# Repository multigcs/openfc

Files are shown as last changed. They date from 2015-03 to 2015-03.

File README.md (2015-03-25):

OpenFC is an new Open-Hardware Flight-Controller

Standard-Size: 50x50mm (45x45mm holes) 

CPU: STM32F405 @ 168MHZ

Gyro/ACC: MPU6000 (SPI)

Compass: HMC5983 (SPI)

Baro: MS5611 (SPI)

Serial-Ports for GPS, Telemetry and SBUS

8 PWM-ESC-Connectors + CAN-Bus

PPM and SBUS inputs

microSD slot

Autoquad software compatible (Board M4r6) (https://code.google.com/p/autoquad/)

Changes v0.9:

	* initial Version
	* 2 errors in the Layout, but working

Changes v0.91: 

	* untested
	* bugfixes of v0.9
	* LED-Postion moved
	* SBUS-Inverter added

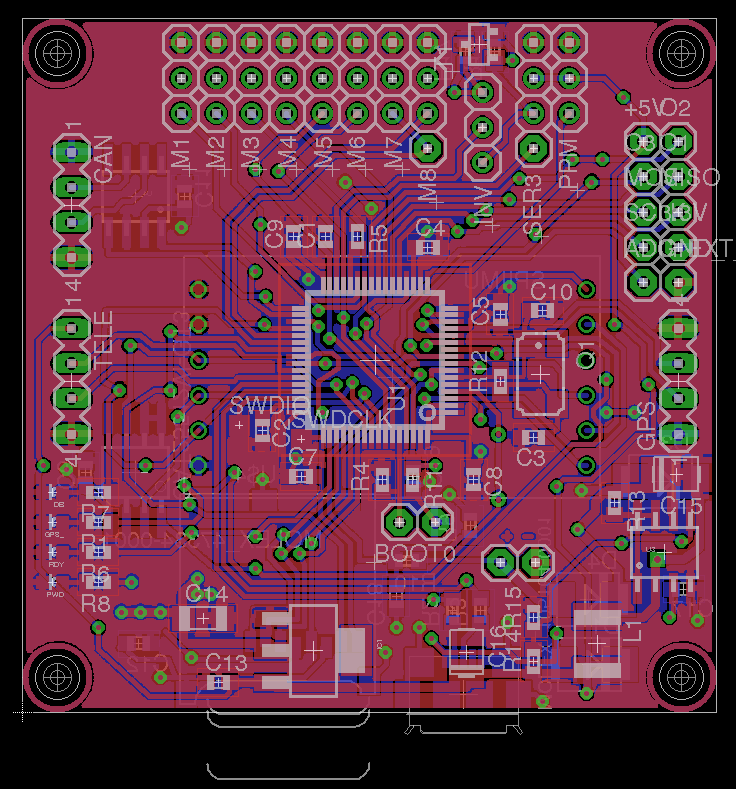
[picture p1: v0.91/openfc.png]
v0.91 Board-Layout


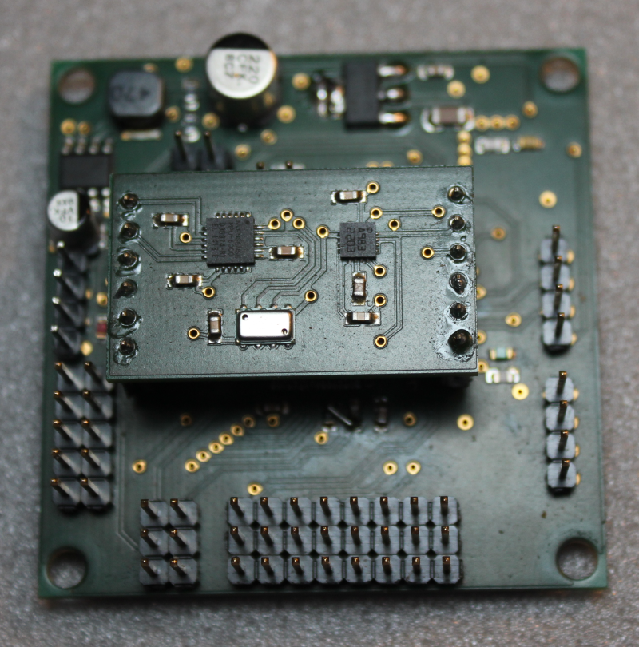
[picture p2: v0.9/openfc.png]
v0.90 Board-Layout v0.9 Board


First IMU-Test: https://www.youtube.com/watch?v=cWaLLEZJb3Y

First Flight-Test: https://www.youtube.com/watch?v=trHpGgnNXYM

First Poshold-Test: https://www.youtube.com/watch?v=XDp27G_Ods4

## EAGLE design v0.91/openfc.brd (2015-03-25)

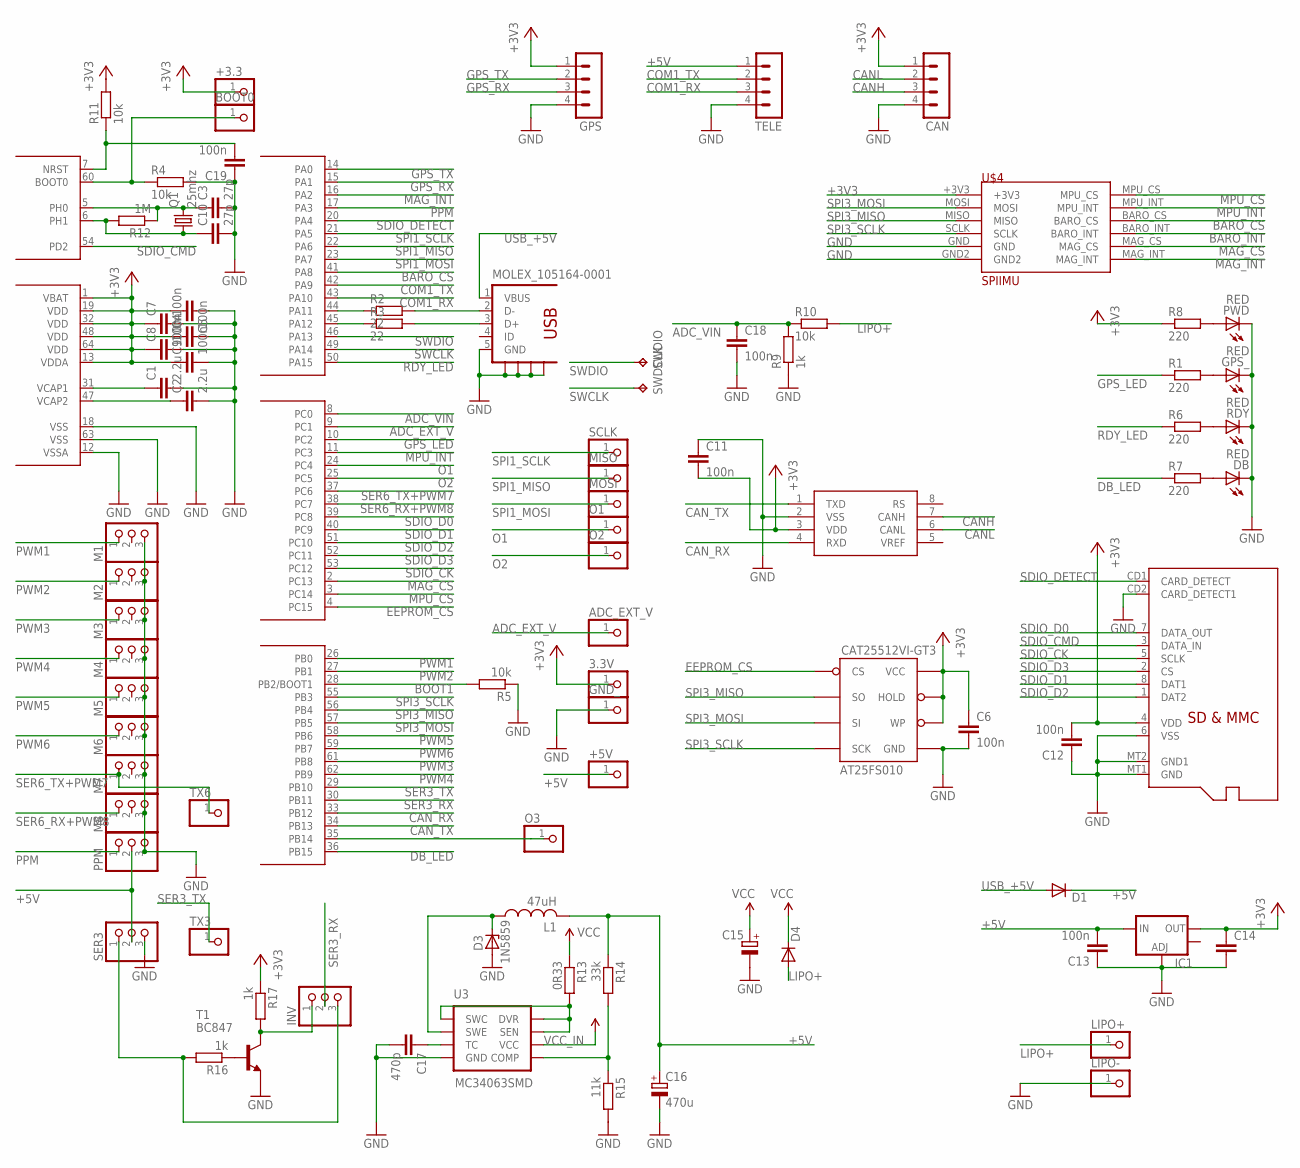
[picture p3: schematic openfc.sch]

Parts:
3.3V: PINHD-1X1; 1X01
+3.3, +5V: PINHD-1X1; 1X01
ADC_EXT_V: PINHD-1X1; 1X01
BOOT0: PINHD-1X1; 1X01
C1, C2: 2.2u; C0603
C3, C10: 27p; C0603
C4, C5, C6, C7, C8, C9, C11, C12, C13, C18, C19: 100n; C0603
C14: C-EUC1206; C1206
C15: CPOL-EUB/3528-21R; B/3528-21R
C16: 470u; B/3528-21R
C17: 470p; C0603
CAN: MA04-1
CAT25512VI-GT3: AT25FS010; SO08WIDE
D1, D4: DIODE-SMB; SMB
D3: 1N5859; SMB
DB: RED; LED-0603
GND_: PINHD-1X1; 1X01
GPS: MA04-1
GPS_: RED; LED-0603
IC1: V_REG_LM1117SOT223; SOT223
INV: PINHD-1X3; 1X03
L1: 47uH; L1812
LIPO+: PINHD-1X1; 1X01
LIPO-: PINHD-1X1; 1X01
M1, M2, M3, M4, M5, M6, M7, M8: PINHD-1X3; 1X03
MISO: PINHD-1X1; 1X01
MOLEX_47334-0001: MICROSD
MOLEX_105164-0001: USB-5P; USB-MINI-B
MOSI: PINHD-1X1; 1X01
O1, O2, O3: PINHD-1X1; 1X01
PPM: PINHD-1X3; 1X03
PWD: RED; LED-0603
Q1: 25mhz; CTS406
R1, R6, R7, R8: 220; R0603
R2, R3: 22; R0603
R4, R5, R10, R11: 10k; R0603
R9, R16, R17: 1k; R0603
R12: 1M; R0603
R13: 0R33; R0603
R14: 33k; R0603
R15: 11k; R0603
RDY: RED; LED-0603
SCLK: PINHD-1X1; 1X01
SER3: PINHD-1X3; 1X03
SWDCLK: TPTP14SQ; TP14SQ
SWDIO: TPTP14SQ; TP14SQ
T1: BC847; SOT23
TELE: MA04-1
TX3, TX6: PINHD-1X1; 1X01
U1: STM32F4-64; SQFP-S-10X10-64
U3: MC34063SMD; SO08
U4: MCP2551; SO08
U$4: SPIIMU

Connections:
+3V3: 3.3V.1, +3.3.1, C4.1, C5.2, C6.1, C7.1, C8.1, C9.1, C11.2, C12.2, C14.1, CAN.1, CAT25512VI-GT3.3 (WP), CAT25512VI-GT3.7 (HOLD), CAT25512VI-GT3.8 (VCC), GPS.1, IC1.2 (OUT), MOLEX_47334-0001.4 (VDD), R8.1, R11.2, R17.1, U1.1 (VBAT), U1.13 (VDDA), U1.19 (VDD), U1.32 (VDD), U1.48 (VDD), U1.64 (VDD), U4.3 (VDD), U$4.+3V3
+5V: +5V.1, C13.2, C16.+, D1.C, IC1.3 (IN), L1.2, PPM.2, R14.1, SER3.2, TELE.1
ADC_EXT_V: ADC_EXT_V.1, U1.9 (PC1)
ADC_VIN: C18.1, R9.2, R10.1, U1.8 (PC0)
BARO_CS: U1.41 (PA8), U$4.BARO_CS
BARO_INT: U$4.BARO_INT
BOOT0: BOOT0.1, R4.1, U1.60 (BOOT0)
BOOT1: R5.2, U1.28 (PB2/BOOT1)
CANH: CAN.3, U4.7 (CANH)
CANL: CAN.2, U4.6 (CANL)
CAN_RX: U1.33 (PB12), U4.4 (RXD)
CAN_TX: U1.34 (PB13), U4.1 (TXD)
COM1_RX: TELE.3, U1.43 (PA10)
COM1_TX: TELE.2, U1.42 (PA9)
DB_LED: R7.1, U1.36 (PB15)
EEPROM_CS: CAT25512VI-GT3.1 (CS), U1.4 (PC15)
GND: C1.2, C2.2, C3.2, C4.2, C5.1, C6.2, C7.2, C8.2, C9.2, C10.2, C11.1, C12.1, C13.1, C14.2, C15.-, C16.-, C17.2, C18.2, C19.1, CAN.4, CAT25512VI-GT3.4 (GND), D3.A, DB.C, GND_.1, GPS.4, GPS_.C, IC1.1 (ADJ), LIPO-.1, M1.3, M2.3, M3.3, M4.3, M5.3, M6.3, M7.3, M8.3, MOLEX_47334-0001.6 (VSS), MOLEX_47334-0001.CD2 (CARD_DETECT1), MOLEX_47334-0001.MT1 (GND), MOLEX_47334-0001.MT2 (GND1), MOLEX_105164-0001.5 (GND), MOLEX_105164-0001.S1, MOLEX_105164-0001.S2, MOLEX_105164-0001.S3, MOLEX_105164-0001.S4, PPM.3, PWD.C, R4.2, R5.1, R9.1, R15.2, RDY.C, SER3.3, T1.2 (E), TELE.4, U1.12 (VSSA), U1.18 (VSS), U1.63 (VSS), U3.4 (GND), U4.2 (VSS), U$4.GND, U$4.GND2
GPS_LED: R1.1, U1.10 (PC2)
GPS_RX: GPS.3, U1.15 (PA1)
GPS_TX: GPS.2, U1.14 (PA0)
LIPO+: D4.A, LIPO+.1, R10.2
MAG_CS: U1.2 (PC13), U$4.MAG_CS
MAG_INT: U1.16 (PA2), U$4.MAG_INT
MPU_CS: U1.3 (PC14), U$4.MPU_CS
MPU_INT: U1.11 (PC3), U$4.MPU_INT
unnamed: C2.1, U1.47 (VCAP2)
unnamed: C1.1, U1.31 (VCAP1)
unnamed: C19.2, R11.1, U1.7 (NRST)
unnamed: PWD.A, R8.2
unnamed: GPS_.A, R1.2
unnamed: R6.2, RDY.A
unnamed: DB.A, R7.2
unnamed: R16.1, T1.1 (B)
unnamed: C3.1, Q1.3 (2), R12.1, U1.5 (PH0)
unnamed: C10.1, Q1.1, R12.2, U1.6 (PH1)
unnamed: R2.1, U1.44 (PA11)
unnamed: R3.1, U1.45 (PA12)
unnamed: C17.1, U3.3 (TC)
unnamed: D3.C, L1.1, U3.2 (SWE)
unnamed: R14.2, R15.1, U3.5 (COMP)
unnamed: R13.2, U3.1 (SWC), U3.7 (SEN), U3.8 (DVR)
O1: O1.1, U1.24 (PC4)
O2: O2.1, U1.25 (PC5)
O3: O3.1, U1.35 (PB14)
PPM: PPM.1, U1.17 (PA3)
PWM1: M1.1, U1.26 (PB0)
PWM2: M2.1, U1.27 (PB1)
PWM3: M3.1, U1.61 (PB8)
PWM4: M4.1, U1.62 (PB9)
PWM5: M5.1, U1.58 (PB6)
PWM6: M6.1, U1.59 (PB7)
RDY_LED: R6.1, U1.50 (PA15)
SDIO_CK: MOLEX_47334-0001.5 (SCLK), U1.53 (PC12)
SDIO_CMD: MOLEX_47334-0001.3 (DATA_IN), U1.54 (PD2)
SDIO_D0: MOLEX_47334-0001.7 (DATA_OUT), U1.39 (PC8)
SDIO_D1: MOLEX_47334-0001.8 (DAT1), U1.40 (PC9)
SDIO_D2: MOLEX_47334-0001.1 (DAT2), U1.51 (PC10)
SDIO_D3: MOLEX_47334-0001.2 (CS), U1.52 (PC11)
SDIO_DETECT: MOLEX_47334-0001.CD1 (CARD_DETECT), U1.20 (PA4)
SER3_RX: INV.2, U1.30 (PB11)
SER3_RX_INV: INV.1, R17.2, T1.3 (C)
SER3_RX_NORM: INV.3, R16.2, SER3.1
SER3_TX: TX3.1, U1.29 (PB10)
SER6_RX+PWM8: M8.1, U1.38 (PC7)
SER6_TX+PWM7: M7.1, TX6.1, U1.37 (PC6)
SPI1_MISO: MISO.1, U1.22 (PA6)
SPI1_MOSI: MOSI.1, U1.23 (PA7)
SPI1_SCLK: SCLK.1, U1.21 (PA5)
SPI3_MISO: CAT25512VI-GT3.2 (SO), U1.56 (PB4), U$4.MISO
SPI3_MOSI: CAT25512VI-GT3.5 (SI), U1.57 (PB5), U$4.MOSI
SPI3_SCLK: CAT25512VI-GT3.6 (SCK), U1.55 (PB3), U$4.SCLK
SWCLK: SWDCLK.TP, U1.49 (PA14)
SWDIO: SWDIO.TP, U1.46 (PA13)
USB_+5V: D1.A, MOLEX_105164-0001.1 (VBUS)
USB_D+: MOLEX_105164-0001.3 (D+), R3.2
USB_D-: MOLEX_105164-0001.2 (D-), R2.2
VCC_IN: C15.+, D4.C, R13.1, U3.6 (VCC)

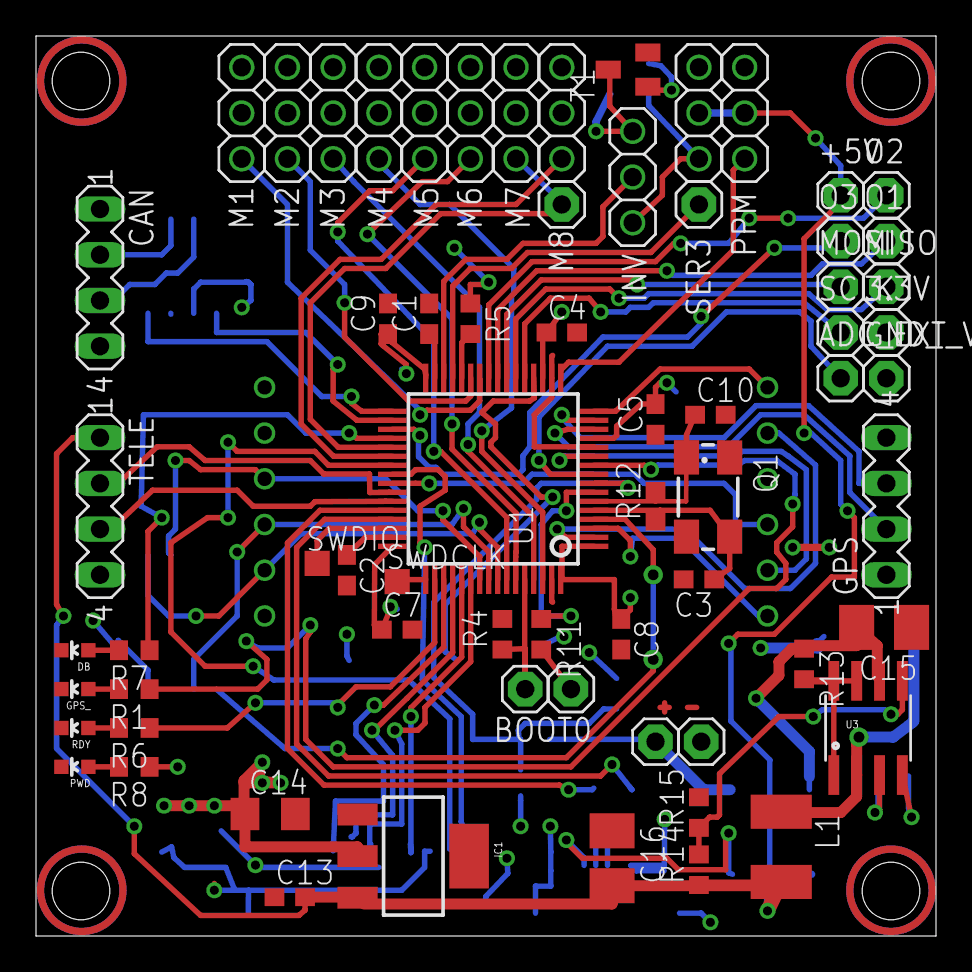
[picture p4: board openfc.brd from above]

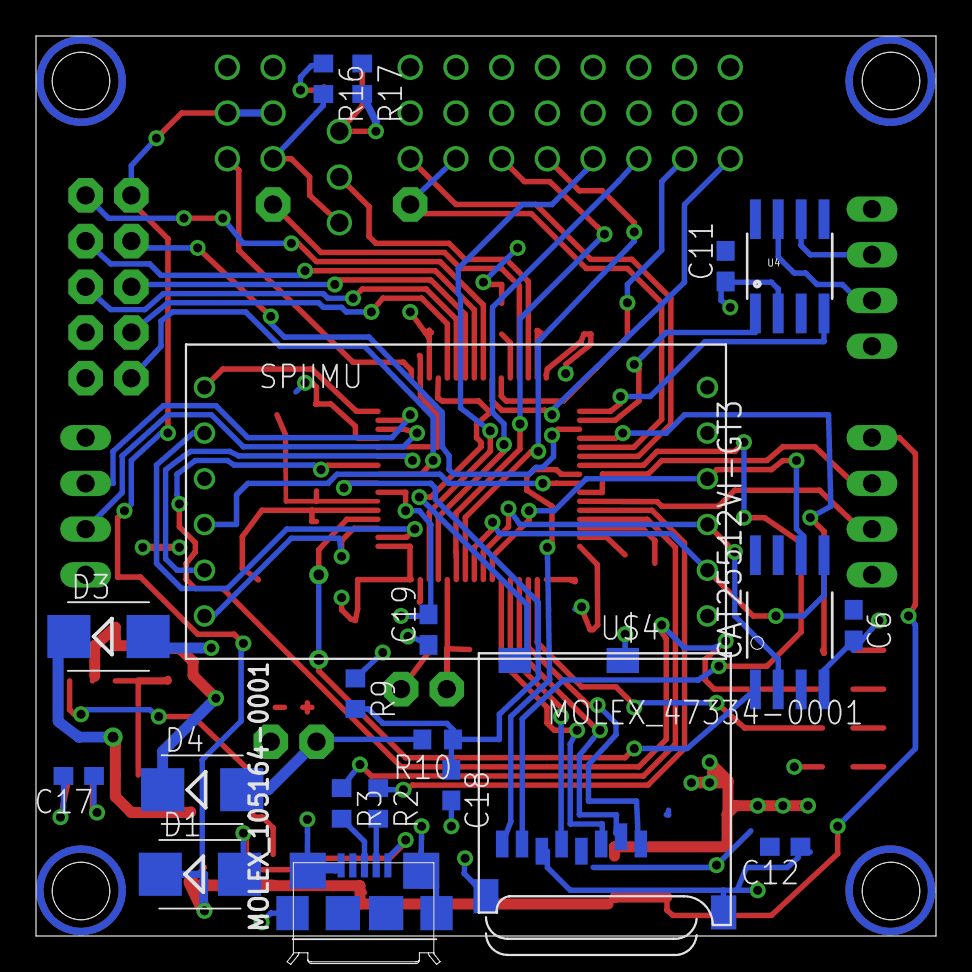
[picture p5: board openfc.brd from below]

Board: 2 copper layers, 50.0 x 50.0 mm, 86 parts (20 on the bottom side), 76 nets.

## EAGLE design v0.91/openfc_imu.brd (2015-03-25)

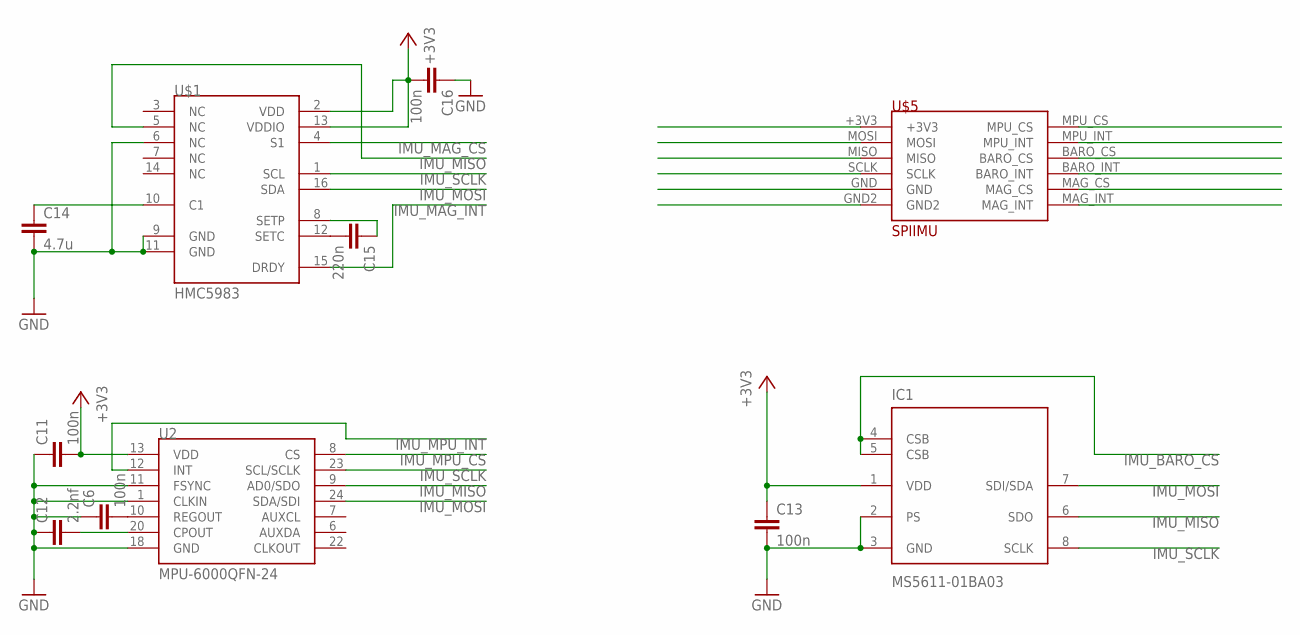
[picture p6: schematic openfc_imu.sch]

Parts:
C6, C11, C13, C16: 100n; C0603
C12: 2.2nf; C0603
C14: 4.7u; C0603
C15: 220n; C0603
IC1: MS5611-01BA03; SON125P300X500X100-8N
U2: MPU-6000QFN-24; QFN-24-TESTING
U$1: HMC5983; 16LPCC
U$5: SPIIMU

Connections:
IMU+3V3: C11.2, C13.1, C16.2, IC1.1 (VDD), U2.13 (VDD), U$1.2 (VDD), U$1.13 (VDDIO), U$5.+3V3
IMU_BARO_CS: IC1.4 (CSB), IC1.5 (CSB), U$5.BARO_CS
IMU_BARO_INT: U$5.BARO_INT
IMU_GND: C6.1, C11.1, C12.1, C13.2, C14.2, C16.1, IC1.2 (PS), IC1.3 (GND), U2.1 (CLKIN), U2.11 (FSYNC), U2.18 (GND), U$1.6 (NC), U$1.9 (GND), U$1.11 (GND), U$5.GND, U$5.GND2
IMU_MAG_CS: U$1.4 (S1), U$5.MAG_CS
IMU_MAG_INT: U$1.15 (DRDY), U$5.MAG_INT
IMU_MISO: IC1.6 (SDO), U2.9 (AD0/SDO), U$1.5 (NC), U$5.MISO
IMU_MOSI: IC1.7 (SDI/SDA), U2.24 (SDA/SDI), U$1.16 (SDA), U$5.MOSI
IMU_MPU_CS: U2.8 (CS), U$5.MPU_CS
IMU_MPU_INT: U2.12 (INT), U$5.MPU_INT
IMU_SCLK: IC1.8 (SCLK), U2.23 (SCL/SCLK), U$1.1 (SCL), U$5.SCLK
unnamed: C6.2, U2.10 (REGOUT)
unnamed: C14.1, U$1.10 (C1)
unnamed: C12.2, U2.20 (CPOUT)
unnamed: C15.1, U$1.8 (SETP)
unnamed: C15.2, U$1.12 (SETC)

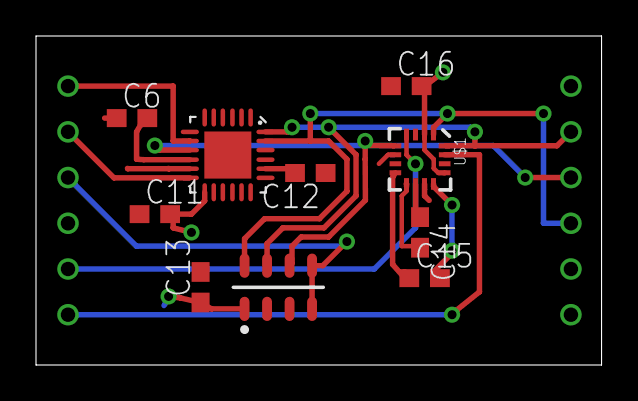
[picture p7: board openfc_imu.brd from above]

Board: 2 copper layers, 31.4 x 18.3 mm, 11 parts (1 on the bottom side), 15 nets.

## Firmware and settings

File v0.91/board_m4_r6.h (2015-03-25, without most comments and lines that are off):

#define _board_h
#define HAS_USB
#define SDIO_DMA			DMA2
#define SDIO_DMA_STREAM			DMA2_Stream3
#define SDIO_DMA_CHANNEL		DMA_Channel_4
#define SDIO_DMA_FLAG_FEIF		DMA_FLAG_FEIF3
#define SDIO_DMA_FLAG_DMEIF		DMA_FLAG_DMEIF3
#define SDIO_DMA_FLAG_TEIF		DMA_FLAG_TEIF3
#define SDIO_DMA_FLAG_HTIF		DMA_FLAG_HTIF3
#define SDIO_DMA_FLAG_TCIF		DMA_FLAG_TCIF3
#define SDIO_DMA_IRQHANDLER		DMA2_Stream3_IRQHandler
#define SDIO_DMA_IRQn			DMA2_Stream3_IRQn
#define SDIO_DETECT_GPIO_PORT		GPIOA
#define SDIO_DETECT_PIN			GPIO_Pin_4
#define SDIO_DETECT_PORT_SOURCE		EXTI_PortSourceGPIOA
#define SDIO_DETECT_PIN_SOURCE		EXTI_PinSource4
#define SDIO_DETECT_IRQ			EXTI4_IRQn
#define SDIO_DETECT_HANDLER		EXTI4_IRQHandler
#define SDIO_DETECT_EXTI_LINE		EXTI_Line4
#define SDIO_TRANSFER_CLK_DIV           ((uint8_t)0x02)	// SDIO Data Transfer Frequency (12MHz max)
enum pwmPorts {
    PWM_1 = 0,
    PWM_2,
    PWM_3,
    PWM_4,
    PWM_5,
    PWM_6,
    PWM_7,
    PWM_8,
    PWM_9,
    PWM_NUM_PORTS
};
#define PPM_PWM_CHANNEL		8	// which PWM channel to use for PPM capture
#define PWM_TIMERS  const TIM_TypeDef *pwmTimers[] = { \
    TIM3, \
    TIM3, \
    TIM4, \
    TIM4, \
    TIM4, \
    TIM4, \
    TIM8, \
    TIM8, \
    TIM9 \
};
#define	PWM_AFS	    const uint8_t pwmAFs[] = { \
    GPIO_AF_TIM3, \
    GPIO_AF_TIM3, \
    GPIO_AF_TIM4, \
    GPIO_AF_TIM4,  \
    GPIO_AF_TIM4, \
    GPIO_AF_TIM4, \
    GPIO_AF_TIM8, \
    GPIO_AF_TIM8, \
    GPIO_AF_TIM9  \
};
#define PWM_PORTS   const GPIO_TypeDef *pwmPorts[] = { \
    GPIOB, \
    GPIOB, \
    GPIOB, \
    GPIOB, \
    GPIOB, \
    GPIOB, \
    GPIOC, \
    GPIOC, \
    GPIOA  \
};
#define PWM_PINS    const uint32_t pwmPins[] = { \
    GPIO_Pin_0, \
    GPIO_Pin_1, \
    GPIO_Pin_8, \
    GPIO_Pin_9, \
    GPIO_Pin_6, \
    GPIO_Pin_7, \
    GPIO_Pin_6, \
    GPIO_Pin_7, \
    GPIO_Pin_3 \
};
#define PWM_PINSOURCES	const uint16_t pwmPinSources[] = { \
    GPIO_PinSource0, \
    GPIO_PinSource1, \
    GPIO_PinSource8, \
    GPIO_PinSource9, \
    GPIO_PinSource6, \
    GPIO_PinSource7, \
    GPIO_PinSource6, \
    GPIO_PinSource7, \
    GPIO_PinSource3 \
};
#define PWM_TIMERCHANNELS   const uint8_t pwmTimerChannels[] = { \
    TIM_Channel_3, \
    TIM_Channel_4, \
    TIM_Channel_3, \
    TIM_Channel_4, \
    TIM_Channel_1, \
    TIM_Channel_2, \
    TIM_Channel_1, \
    TIM_Channel_2, \
    TIM_Channel_2 \
};
#define PWM_BDTRS   const uint8_t pwmBDTRs[] = { \
    0, \
    0, \
    0, \
    0, \
    0, \
    0, \
    1, \
    1, \
    0 \
};
#define PWM_CLOCKS  const uint32_t pwmClocks[] = { \
    84000000, \
    84000000, \
    84000000, \
    84000000, \
    84000000, \
    84000000, \
    168000000, \
    168000000, \
    168000000 \
};
#define PWM_IC_IRQS  const uint8_t pwmIcIrqChannels[] = { \
    TIM3_IRQn, \
    TIM3_IRQn, \
    TIM4_IRQn, \
    TIM4_IRQn, \
    TIM4_IRQn, \
    TIM4_IRQn, \
    TIM8_CC_IRQn, \
    TIM8_CC_IRQn, \
    TIM1_BRK_TIM9_IRQn \
};
#define PWM_IRQ_TIM3_CH3	0
#define PWM_IRQ_TIM3_CH4	1
#define PWM_IRQ_TIM4_CH3	2
#define PWM_IRQ_TIM4_CH4	3
#define PWM_IRQ_TIM4_CH1	4
#define PWM_IRQ_TIM4_CH2	5
#define PWM_IRQ_TIM8_CH1	6
#define PWM_IRQ_TIM8_CH2	7
#define PWM_IRQ_TIM9_CH2	8
#define RC1_DELTANG_BAUD	134078
#define RC1_UART		USART3
#define RC2_UART		USART2
#define SUPERVISOR_READY_PORT	GPIOA
#define SUPERVISOR_READY_PIN	GPIO_Pin_15
#define SUPERVISOR_DEBUG_PORT	GPIOB
#define SUPERVISOR_DEBUG_PIN	GPIO_Pin_15
#define GPS_USART		UART4
#define GPS_LED_PORT		GPIOC
#define GPS_LED_PIN		GPIO_Pin_2
#define ADC_DMA_STREAM		DMA2_Stream4
#define ADC_DMA_CHANNEL		DMA_Channel_0
#define ADC_DMA_FLAGS		(DMA_IT_TEIF4 | DMA_IT_DMEIF4 | DMA_IT_FEIF4 | DMA_IT_TCIF4 | DMA_IT_HTIF4)
#define ADC_DMA_TC_FLAG		DMA_IT_TCIF4
#define ADC_DMA_ISR		DMA2->HISR
#define ADC_DMA_CR		DMA2->HIFCR
#define ADC_DMA_IRQ		DMA2_Stream4_IRQn
#define ADC_DMA_HANDLER		DMA2_Stream4_IRQHandler
#define CANx			    CAN2
#define CAN_CLK			    (RCC_APB1Periph_CAN1 | RCC_APB1Periph_CAN2)
#define CAN_GPIO_PORT		    GPIOB
#define CAN_RX_PIN		    GPIO_Pin_12
#define CAN_TX_PIN		    GPIO_Pin_13
#define CAN_AF_PORT		    GPIO_AF_CAN2
#define CAN_RX_SOURCE		    GPIO_PinSource12
#define CAN_TX_SOURCE		    GPIO_PinSource13
#define CAN_RX0_IRQ		    CAN2_RX0_IRQn
#define CAN_RX0_HANDLER		    CAN2_RX0_IRQHandler
#define CAN_TX_IRQ		    CAN2_TX_IRQn
#define CAN_TX_HANDLER		    CAN2_TX_IRQHandler
#define SPI_SPI1_CLOCK		    RCC_APB2Periph_SPI1
#define SPI_SPI1_AF		    GPIO_AF_SPI1
#define SPI_SPI1_SCK_PORT	    GPIOA
#define SPI_SPI1_MISO_PORT	    GPIOA
#define SPI_SPI1_MOSI_PORT	    GPIOA
#define SPI_SPI1_SCK_PIN	    GPIO_Pin_5
#define SPI_SPI1_MISO_PIN	    GPIO_Pin_6
#define SPI_SPI1_MOSI_PIN	    GPIO_Pin_7
#define SPI_SPI1_SCK_SOURCE	    GPIO_PinSource5
#define SPI_SPI1_MISO_SOURCE	    GPIO_PinSource6
#define SPI_SPI1_MOSI_SOURCE	    GPIO_PinSource7
#define SPI_SPI1_DMA_RX		    DMA2_Stream0
#define SPI_SPI1_DMA_RX_CHANNEL	    DMA_Channel_3
#define SPI_SPI1_DMA_RX_FLAGS	    (DMA_IT_TEIF0 | DMA_IT_DMEIF0 | DMA_IT_FEIF0 | DMA_IT_TCIF0 | DMA_IT_HTIF0)
#define SPI_SPI1_DMA_RX_IRQ	    DMA2_Stream0_IRQn
#define SPI_SPI1_DMA_RX_HANDLER	    DMA2_Stream0_IRQHandler
#define SPI_SPI1_DMA_TX		    DMA2_Stream5
#define SPI_SPI1_DMA_TX_CHANNEL	    DMA_Channel_3
#define SPI_SPI1_DMA_TX_FLAGS	    (DMA_IT_TEIF5 | DMA_IT_DMEIF5 | DMA_IT_FEIF5 | DMA_IT_TCIF5 | DMA_IT_HTIF5)
#define SPI_SPI3_CLOCK		    RCC_APB1Periph_SPI3
#define SPI_SPI3_AF		    GPIO_AF_SPI3
#define SPI_SPI3_SCK_PORT	    GPIOB
#define SPI_SPI3_MISO_PORT	    GPIOB
#define SPI_SPI3_MOSI_PORT	    GPIOB
#define SPI_SPI3_SCK_PIN	    GPIO_Pin_3
#define SPI_SPI3_MISO_PIN	    GPIO_Pin_4
#define SPI_SPI3_MOSI_PIN	    GPIO_Pin_5
#define SPI_SPI3_SCK_SOURCE	    GPIO_PinSource3
#define SPI_SPI3_MISO_SOURCE	    GPIO_PinSource4
#define SPI_SPI3_MOSI_SOURCE	    GPIO_PinSource5
#define SPI_SPI3_DMA_RX		    DMA1_Stream0
#define SPI_SPI3_DMA_RX_CHANNEL	    DMA_Channel_0
#define SPI_SPI3_DMA_RX_FLAGS	    (DMA_IT_TEIF0 | DMA_IT_DMEIF0 | DMA_IT_FEIF0 | DMA_IT_TCIF0 | DMA_IT_HTIF0)
#define SPI_SPI3_DMA_RX_IRQ	    DMA1_Stream0_IRQn
#define SPI_SPI3_DMA_RX_HANDLER	    DMA1_Stream0_IRQHandler
#define SPI_SPI3_DMA_TX		    DMA1_Stream5
#define SPI_SPI3_DMA_TX_CHANNEL	    DMA_Channel_0
#define SPI_SPI3_DMA_TX_FLAGS	    (DMA_IT_TEIF5 | DMA_IT_DMEIF5 | DMA_IT_FEIF5 | DMA_IT_TCIF5 | DMA_IT_HTIF5)
#define HAS_DIGITAL_IMU
#define USE_DIGITAL_IMU
#define DIMU_HAVE_MPU6000
#define DIMU_HAVE_HMC5983
#define DIMU_HAVE_MS5611
#define MPU6000_ACC_SCALE           16     // g      (2, 4, 8, 16)
#define MPU6000_GYO_SCALE           2000  // deg/s  (250, 500, 1000, 2000)
#define DIMU_ORIENT_ACC_X	    (+in[0])
#define DIMU_ORIENT_ACC_Y	    (-in[1])
#define DIMU_ORIENT_ACC_Z	    (-in[2])
#define DIMU_ORIENT_GYO_X	    (-in[0])
#define DIMU_ORIENT_GYO_Y	    (+in[1])
#define DIMU_ORIENT_GYO_Z	    (-in[2])
#define DIMU_ORIENT_MAG_X	    (-in[0])
#define DIMU_ORIENT_MAG_Y	    (+in[1])
#define DIMU_ORIENT_MAG_Z	    (-in[2])
#define DIMU_EEPROM_SPI		    SPI3
#define DIMU_EEPROM_CS_PORT	    GPIOC
#define DIMU_EEPROM_CS_PIN	    GPIO_Pin_15
#define DIMU_HMC5983_SPI	    SPI3
#define DIMU_HMC5983_CS_PORT	    GPIOC
#define DIMU_HMC5983_CS_PIN	    GPIO_Pin_13
#define DIMU_HMC5983_INT_PORT	    GPIOA
#define DIMU_HMC5983_INT_PIN	    GPIO_Pin_2
#define DIMU_HMC5983_INT_EXTI_PORT  EXTI_PortSourceGPIOA
#define DIMU_HMC5983_INT_EXTI_PIN   EXTI_PinSource2
#define DIMU_HMC5983_INT_EXTI_LINE  EXTI_Line2
#define DIMU_HMC5983_INT_EXTI_IRQ   EXTI2_IRQn
#define DIMU_HMC5983_INT_ISR	    EXTI2_IRQHandler
#define DIMU_MS5611_SPI		    SPI3
#define DIMU_MS5611_CS_PORT	    GPIOA
#define DIMU_MS5611_CS_PIN	    GPIO_Pin_8
#define DIMU_MPU6000_SPI	    SPI3
#define DIMU_MPU6000_CS_PORT	    GPIOC
#define DIMU_MPU6000_CS_PIN	    GPIO_Pin_14
#define DIMU_MPU6000_INT_PORT	    GPIOC
#define DIMU_MPU6000_INT_PIN	    GPIO_Pin_3
#define DIMU_MPU6000_INT_EXTI_PORT  EXTI_PortSourceGPIOC
#define DIMU_MPU6000_INT_EXTI_PIN   EXTI_PinSource3
#define DIMU_MPU6000_INT_EXTI_LINE  EXTI_Line3
#define DIMU_MPU6000_INT_EXTI_IRQ   EXTI3_IRQn
#define DIMU_MPU6000_INT_ISR	    EXTI3_IRQHandler
#define COMM_PORT1		    USART1	    // expansion header J2:8, J2:9
#define SERIAL_UART1_PORT	GPIOA
#define SERIAL_UART1_RX_PIN	GPIO_Pin_10
#define SERIAL_UART1_TX_PIN	GPIO_Pin_9
#define SERIAL_UART1_RX_SOURCE	GPIO_PinSource10
#define SERIAL_UART1_TX_SOURCE	GPIO_PinSource9
#define SERIAL_UART1_RX_DMA_ST	DMA2_Stream2
#define SERIAL_UART1_TX_DMA_ST	DMA2_Stream7
#define SERIAL_UART1_RX_DMA_CH	DMA_Channel_4
#define SERIAL_UART1_TX_DMA_CH	DMA_Channel_4
#define SERIAL_UART1_TX_DMA_IT	DMA2_Stream7_IRQHandler
#define SERIAL_UART1_TX_IRQn	DMA2_Stream7_IRQn
#define SERIAL_UART1_RX_TC_FLAG	DMA_FLAG_TCIF2
#define SERIAL_UART1_RX_HT_FLAG	DMA_FLAG_HTIF2
#define SERIAL_UART1_RX_TE_FLAG	DMA_FLAG_TEIF2
#define SERIAL_UART1_RX_DM_FLAG	DMA_FLAG_DMEIF2
#define SERIAL_UART1_RX_FE_FLAG	DMA_FLAG_FEIF2
#define SERIAL_UART1_TX_TC_FLAG	DMA_FLAG_TCIF7
#define SERIAL_UART1_TX_HT_FLAG	DMA_FLAG_HTIF7
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

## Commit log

2015-03-25 add version 0.9
    [openfc.brd, openfc.sch, openfc_imu.brd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]
2015-03-25 add version 0.91
    [openfc.brd, openfc.sch, openfc_imu.brd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]
2015-03-25 add modified board-configuration files for autoquad

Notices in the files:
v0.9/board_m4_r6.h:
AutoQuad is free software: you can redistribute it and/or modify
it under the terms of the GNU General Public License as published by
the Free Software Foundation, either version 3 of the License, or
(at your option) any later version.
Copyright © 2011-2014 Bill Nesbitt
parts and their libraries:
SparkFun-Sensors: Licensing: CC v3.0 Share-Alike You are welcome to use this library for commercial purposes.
